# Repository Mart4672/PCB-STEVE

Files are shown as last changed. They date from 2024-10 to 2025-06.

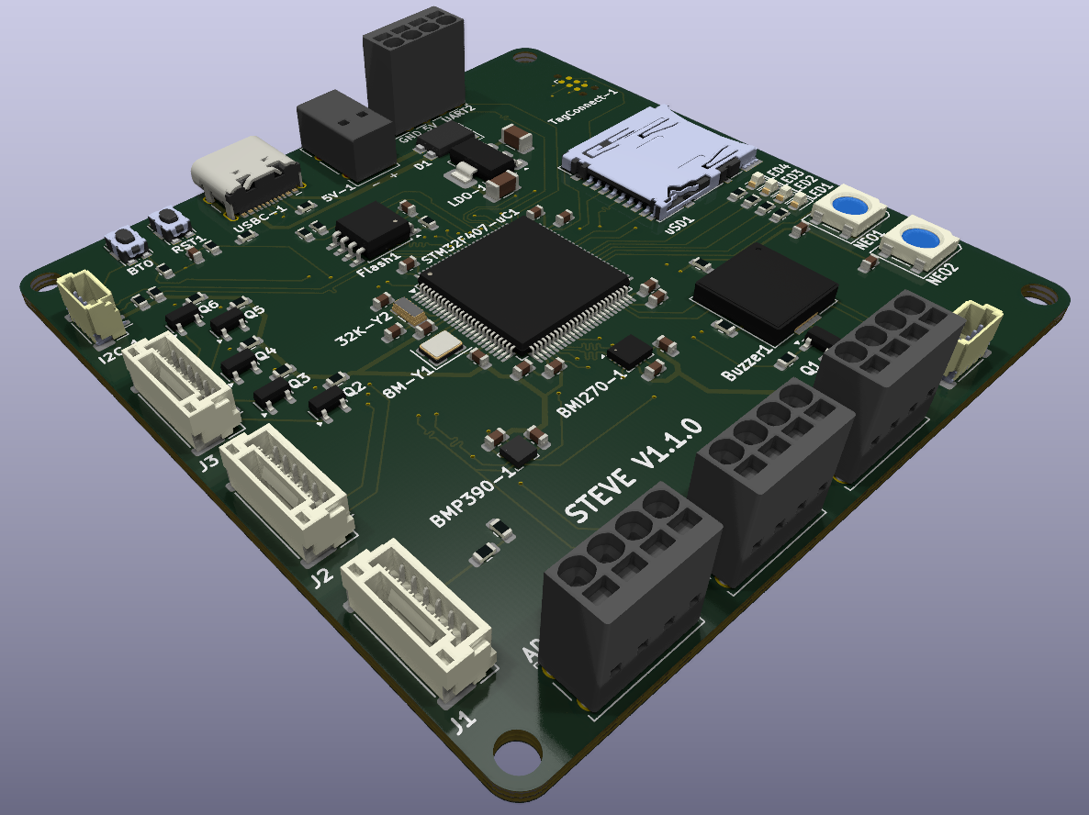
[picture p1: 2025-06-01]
hardware/share/STEVE_V1.1.0/STEVE-1.1.0_3D_Front_45deg.png

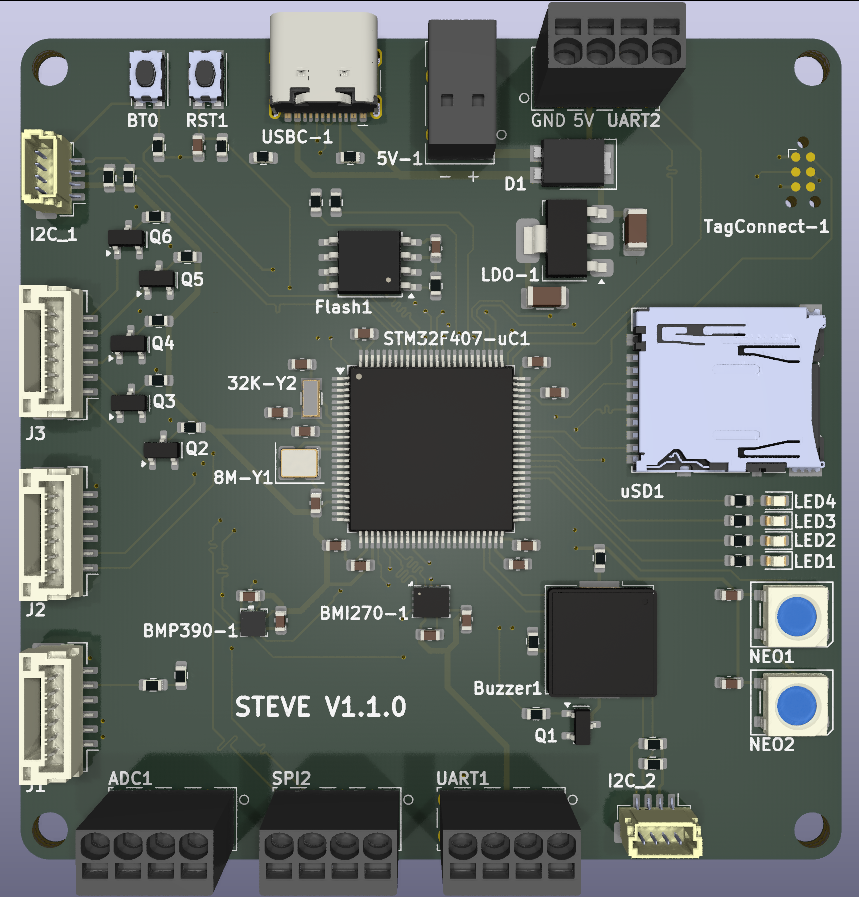
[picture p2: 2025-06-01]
hardware/share/STEVE_V1.1.0/STEVE-1.1.0_3D_Front.png

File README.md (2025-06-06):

# PCB-STEVE
STM32F4 based Flight Computer Development PCB

STEVE, the name of this flight computer, is an acronym:
*Starter Testbed for Evolving the Vehicle Electronics*

As the name implies, the intention of STEVE is to be a testbed circuitboard for proving out avionics functionality.
STEVE is very much a development board as this is the first STM32 PCB that I have designed.

Future versions of STEVE will have a focus on exapnding a flight vehicle's envelope 
(Starter Testbed for Expanding the Vehicle Envelope)

STEVE is intended to be used on a flight vehicle such as a model rocket but can also be used in static environments such as a ground test stand.

## STEVE Version 1.1.0 Hardware Features
- 70 x 70 mm, 6 layer board with all components on one side for ease of manufacturing
- 1 STM32F407 Microcontroller
    - (STM32F407VGT6 is the specific SKU being used)
    - 1024 KB (1MB) of internal flash memory
    - 192 (112+16+64) KB of system RAM
- Reset and Boot buttons
- USB-C input for programming the microcontroller
    - the GCT USB4105-GF-A connector is allegedly rated for 5A
    - also usable for power when not connected to the PSM board
- Terminal block for 5V regulated input
- Micro SD card
- Winbond W25Q 128 Mbit (16 MB) external flash storage
- 1 BMI270 Inertial Measurement Unit (IMU) connected over SPI
- 1 BMP390 Barometric Pressure Sensor connected over SPI
- A 2x5 1.27mm pitch debug header
- A 32.768 kHz Low Speed External Crystal Oscillator
- A 8 MHz High Speed External Crystal Oscillator
- A TI TLV1117 1A 3.3V Output Linear Regulator
- A dedicated telemetry modem connection
    - uses screwless terminal blocks or a JST-GH connector
        - (each JST-GH connection is rated for 1A and the RFD900 has a max draw of ~1A at 5V)
    - GND, 5V, and UART signals (RX and TX) are present
    - placed close to both the USB-C and Regulated 5V power inputs
- 2 JST-SH 4 pin connectors for I2C
    - allows for easy hardware development for I2C devices (load cells, GNSS, etc)
- 1 passive buzzer (passive buzzers allow for different beep noises)
- 4 standard LEDs
- 2 WS2812 (NeoPixel) Addressable LEDs
- Additional GPIO and bus pins broken out
    - SPI2 (also used for BMP390) pins
    - UART1 pins
    - 2 ADC (12-bit) capable pins
    - Uses screwless terminal blocks
- Connectors for PSM board signals (3 x 6 pin connectors)
    - Uses JST-GH connectors
    - Servo PWM signals (4)
    - Mosfet gate signals (5)
    - Mosfet continuity signals (5)
    - Battery #1 Voltage sense line

## Future Updates

### Future STEVE Updates
- use a 3.3V plane on layer 5 (some signals ok) if doing a 6 layer board with components on 1 side
- move the 5V components to the same area
- make the board smaller (60 x 60 mm)
- consider moving the complicated components (BMI, BMP, WS2812) to a separate board
    - probably a bad idea since creating a simple daughter board with Standard PCBA would cost at least (10 PCB + 30 PCBA + 25 shipping) = $65
    - using Economic PCBA only saves ~$25
- give serious consideration to creating a STEVE revision with the PSM circuitry on the same board
    - keep in mind that any board orders also have tarrifs, taxes, and shipping applied, which can easily double the initial PCB/PCBA cost
- use a PMOS mosfet for reverse polarity protection
- add an RJ45 connector to utilize the ethernet capabilities of the STM32F407 (this might be part of a completely different board design)

## Using/opening this project on a different machine

- open the project file in KiCad

On the top bar, the following thing needs to be updated based on the machine you are using:
- Preferences > Configure Paths
Add an enironment variable with a name of:
CURRENT_PROJ_DIR
The value of the enirnment variable should be:
your-repo-dir-path/PCB-STEVE/hardware

On the top bar, the following things should not need to be updated but both use the CURRENT_PROJ_DIR variable 
- Preferences > Manage Symbol Libraries > Project Specific Libraries (tab)
- Preferences > Manage Footprint Libraries > Project Specific Libraries (tab)

## PCB Ordering Notes

#### STEVE V1.1.0 
STEVE V1.1.0 is a 6 layer PCB that uses vias as small as 
0.3mm (hole size) / 0.45mm (overall via diameter)

On JLC's website, 6 layer boards use the "Advanced PCB/PCBA service".
This has different default options from the standard service

Nonstandard options chosen for the advanced PCB service:

- (optional) Specify Stackup > No requirement
- Mark on PCB = 2D barcode (Serial Number)
    - 2D barcode Only | QR Code | STEVE_V1-1-0_SN | Remove Unique Number | 0001 
        - 8*8mm (5x5 also ok) | Specify Position (No Requirement is ok too)

Advanced Options
- $0.71 Blank Box

PCB Assembly Options
A board with 6 or fewer layers and single sided assembly qualifies for 
JLC's Economic PCBA
https://jlcpcb.com/capabilities/pcb-assembly-capabilities
See the above link for Economic PCBA constraints such as
- only supporting green silkscreens
- only supporting the ENIG finish

STEVE 1.1.0 is a 70 x 70mm board; using Standard PCBA auotmatically sets the 
board size to at least 70x70mm for adding edge rails/fiducials.
"The board size would be modified to be 80*70mm for Standard PCBA due to adding two 5mm edge rails on the shorter sides"

Nonstandard PCBA options chosen:
- PCBA Qty = 2 (can choose 2+ based on component availibility)
- Edge Rails/Fiducials = Added by JLCPCB (default)
- Confirm Parts Placement = Yes

Advanced Options
- Photo Confirmation = Yes (Not available for Economic)
- Conformal Coating (+cleaning) = No (can choose yes for future boards)
    - Not available for Economic PCBA
- Packaging = ESD+Cardboard (Cardboard is ok too)
- Solder Paste = Sn96.5/Ag3.0/Cu0.5 (Do NOT use Bismuth/Bi solder)
- The "Bake Components" option is not available for Economic PCBA
    - Will need to use the Standard PCBA service or omit the WS2812 LEDs (C2761795) from being assembled since they are moisture sensitive
- The BMI270 and BMP390 also require Standard PCBA

"Note: The setup fee is $25 per assembly side for Standard PCBA."

Stencil Order Options
- No stencil being ordered
    - If boards with many small pitch components (ex: STM32) are going to be assembled, a reflow oven is strongly recommended
    - if a stencil is ordered, make sure to get it cut to size to save on shipping costs

## Other Notes
- Don't use special characters such as "µ" for part designators, footprints, or values as this can cause issues with processing the bom and positions (CPL) files.

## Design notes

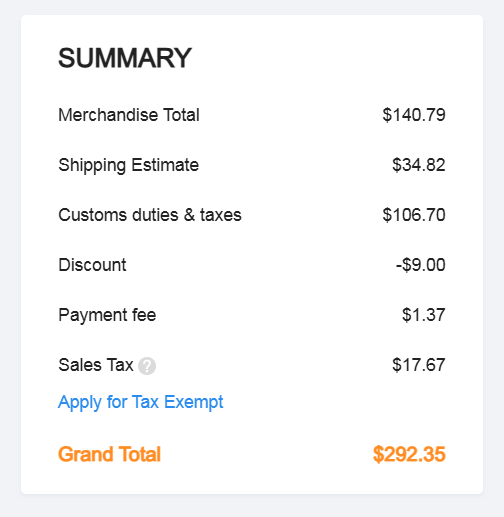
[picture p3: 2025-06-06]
hardware/production/STEVE-1.1.0/STEVE-1.1.0-Quote-JLC/2025-06-01_JLC_PCBA_Quote_Part4_grand_total.png

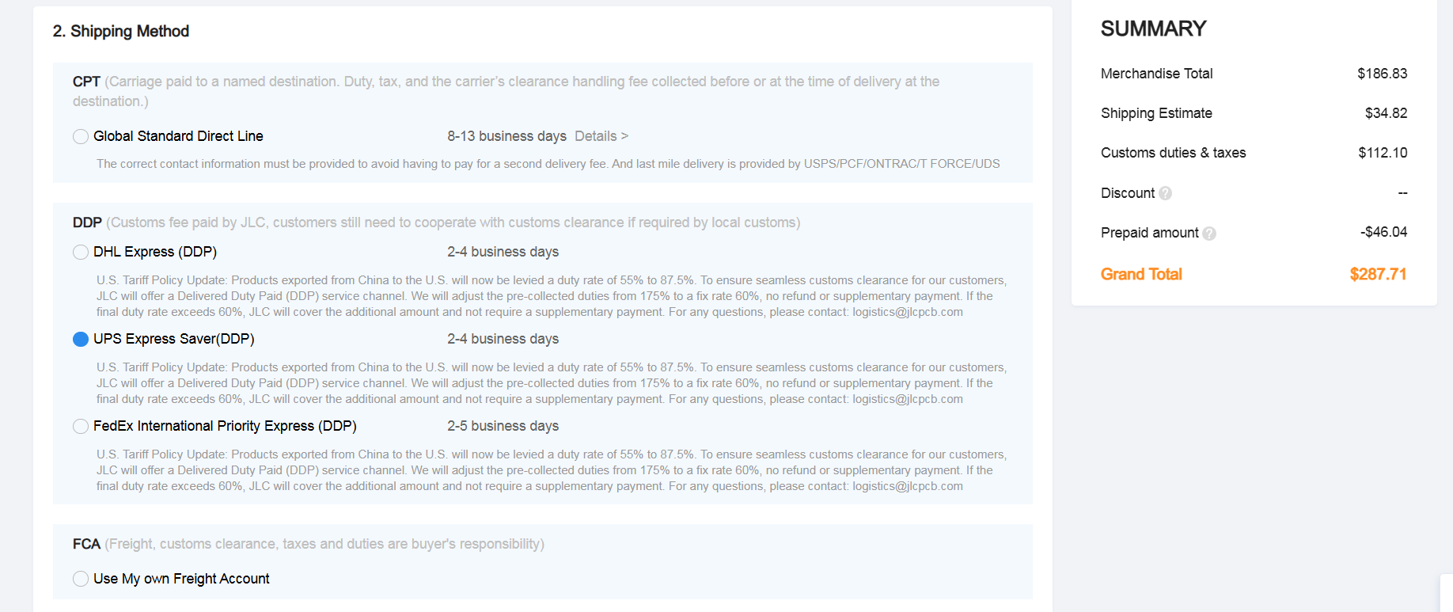
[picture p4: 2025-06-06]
hardware/production/STEVE-1.1.0/STEVE-1.1.0-Quote-JLC/2025-06-01_JLC_PCBA_Quote_Part3_tarrifs.png

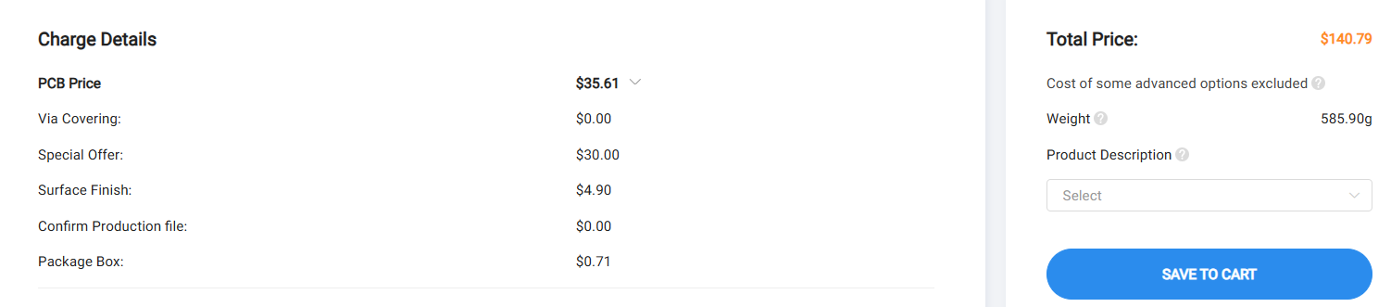
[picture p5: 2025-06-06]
hardware/production/STEVE-1.1.0/STEVE-1.1.0-Quote-JLC/2025-06-01_JLC_PCBA_Quote_Part1.png

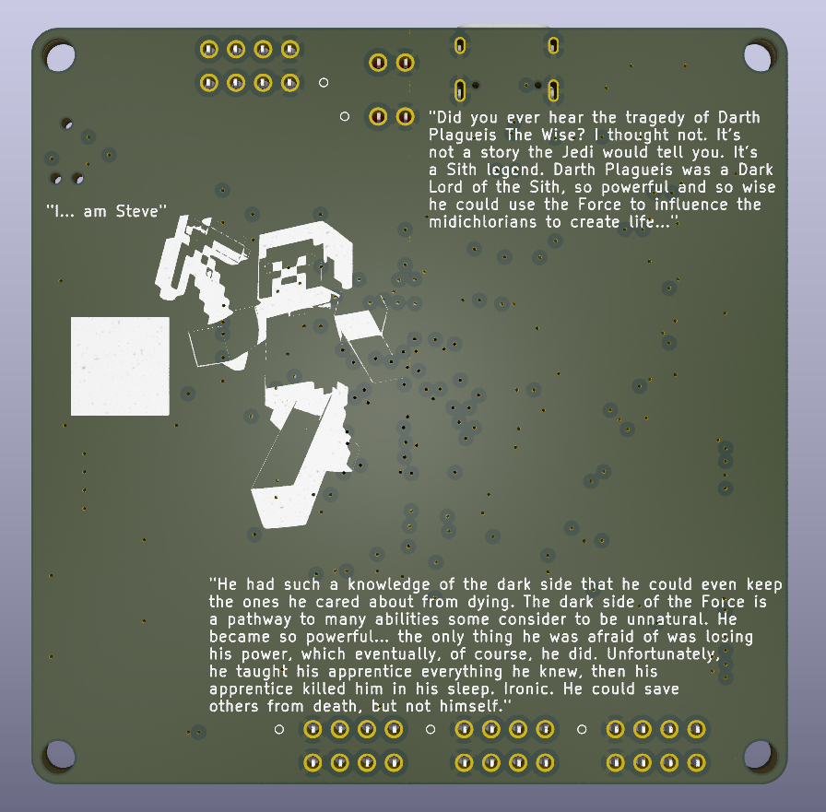
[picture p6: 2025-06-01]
hardware/share/STEVE_V1.1.0/STEVE-1.1.0_3D_Back.png

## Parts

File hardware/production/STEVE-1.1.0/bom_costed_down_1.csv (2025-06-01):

Designator | Footprint | Quantity | Value | LCSC Part #
32K-Y2 | Crystal_SMD_3215-2Pin_3.2x1.5mm_Fixed | 1 | 32.768kHz Crystal 12.5pf C90944
8M-Y1 | Crystal_SMD_3225-4Pin_3.2x2.5mm | 1 | 8MHz Crystal 10pf C400090
BMI270-1 | Bosch_LGA-14_3x2.5mm_P0.5mm | 1 | BMI270 Inertial Measurement Unit C2836813
BMP390-1 | QFN_BMP388_BOS | 1 | BMP390 Barometric Pressure Sensor C2684802
BT0, RST1 | SW_Push_3D_1P1T-SH_NO_CK_KMR2xxG | 2 | Button KMR221G C72443
BUZZER1 | Buzzer_Murata_PKMCS0909E | 1 | Externally Driven Buzzer 1.5-12.5V 4kHz 65dB C910763
C1, C2 | 0603 | 2 | 2.2uF
C10, C11, C27, C28, C29, C30, C31, C32, C33, C7, C8, C9 | 0603 | 12 | 0.1uF
C12 | 0603 | 1 | 4.7uF
C13, C14 | 0603 | 2 | 1.0uF
C25, C26 | 1206 | 2 | 1.0uF
C5, C6 | 0603 | 2 | 5pF
D1 | PDS1040CTL-13_PowerDI-5 | 1 | 10A/5A Schottky Diode Arr C780876
FLASH1 | SOIC-8_5.23x5.23mm_P1.27mm_3D | 1 | W25Q128JVSIQ 128Mb SPI Flash C97521
I2C_1, I2C_2 | JST-SH_BM04B-SRSS-TB_1x04_Vertical_P1.00mm | 2 | JST-SH-4P Vertical C160390
J1, J2, J3 | JST_GH_BM06B-GHS-TBT_1x06-1MP_P1.25mm_Vertical | 3 | JST GH 6P Vertical 1A C189892
LDO-1 | SOT-223-3_TabPin2 | 1 | 3.3V 1A Lin Reg C15578
LED1 | 0603 | 1 | RED
LED2 | 0603 | 1 | YELLOW
LED3 | 0603 | 1 | GREEN
LED4 | 0603 | 1 | BLUE
NEO1, NEO2 | LED_WS2812B_PLCC4_5.0x5.0mm_P3.2mm | 2 | WS2812B RGB LED C2761795
Q1, Q2, Q3, Q4, Q5, Q6 | SOT-23 | 6 | NMOS GSD 350mA 60V C282405
R1, R15 | 0603 | 2 | 100k
R11, R12 | 0603 | 2 | 22
R13, R14 | 0603 | 2 | 5.1k
R16, R17, R18, R19 | 0603 | 4 | 2k
R2 | 0603 | 1 | 4.7k
R20, R21, R22, R26 | 0603 | 4 | 1k
R23, R24, R25 | 0603 | 3 | 220
R3, R4, R5, R6, R7 | 0603 | 5 | 10k
R8 | 0603 | 1 | 422k 1%
R9 | 0603 | 1 | 100k 0.5%
STM32F407-UC1 | LQFP-100_14x14mm_P0.5mm | 1 | STM32F407VGTx Microcontroller C12345
USBC-1 | USB_C_Receptacle_3D_HCTL_HC-TYPE-C-16P-01A | 1 | USB-C Receptacle 16P C3025063
USD1 | microSD_3D_HC_Hirose_DM3AT-SF-PEJM5 | 1 | MicroSD Hirose DM3AT C114218

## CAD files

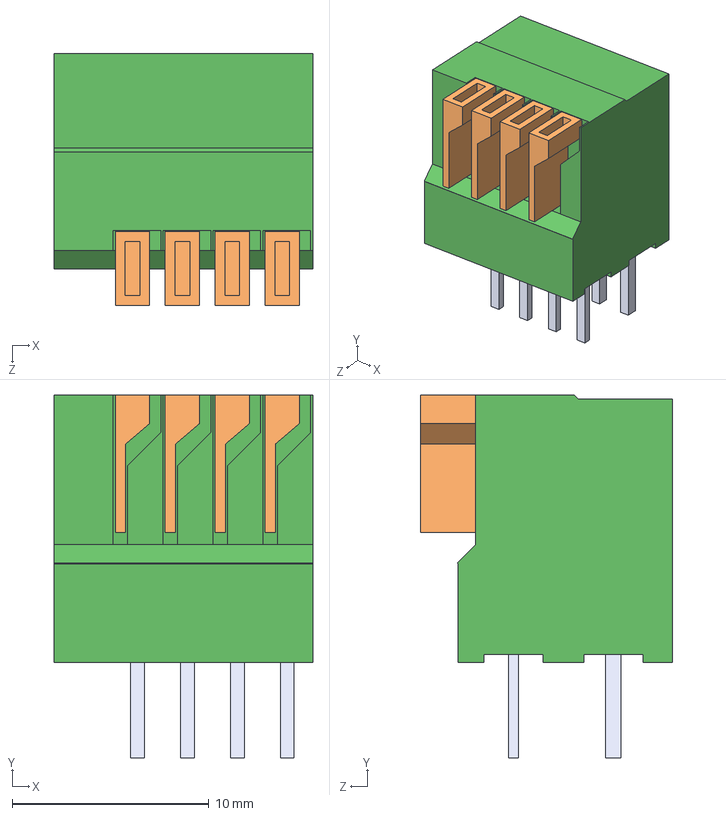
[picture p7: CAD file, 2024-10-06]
hardware/imports/1_2834015_4/1-2834015-4.step
13.2 x 18.5 x 12.8 mm

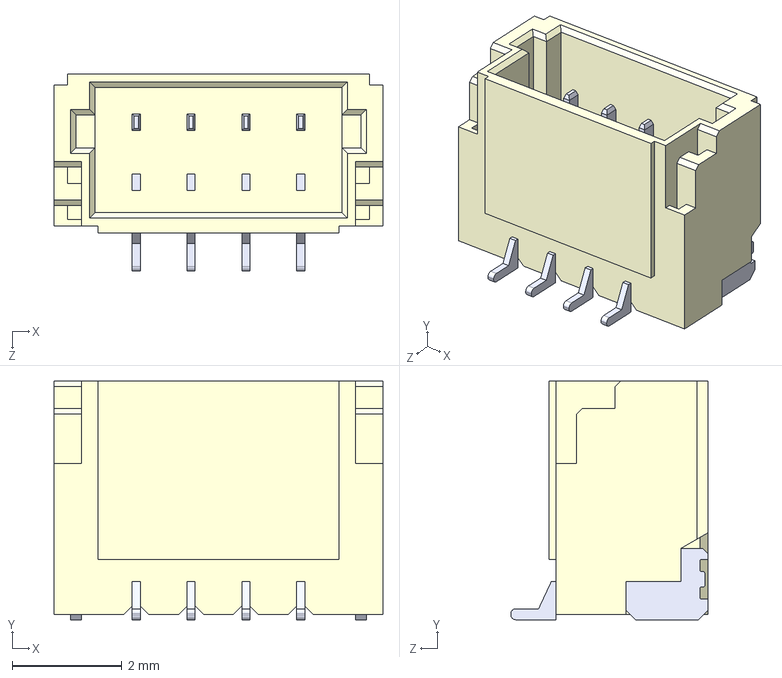
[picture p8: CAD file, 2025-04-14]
hardware/imports/BM04B-SRSS-TB/BM04B-SRSS-TB.STEP
6.00 x 4.35 x 3.60 mm

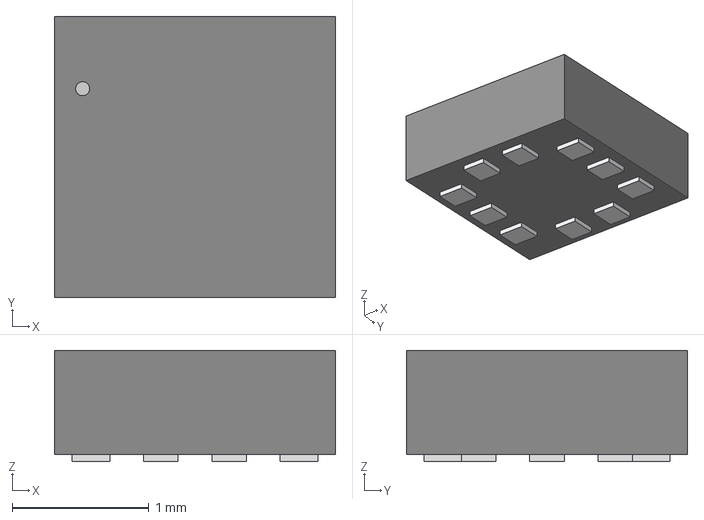
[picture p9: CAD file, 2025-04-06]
hardware/imports/BMP388/QFN_BMP388_BOS.step
2.06 x 2.06 x 0.815 mm

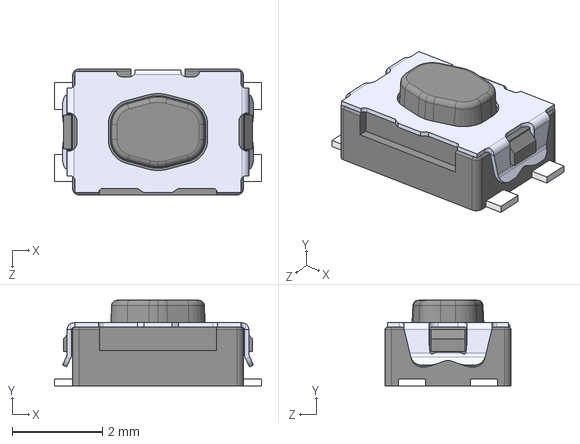
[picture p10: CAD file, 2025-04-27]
hardware/imports/Button_KMR221G_LFS/KMR221G LFS.STEP
4.60 x 1.90 x 2.80 mm

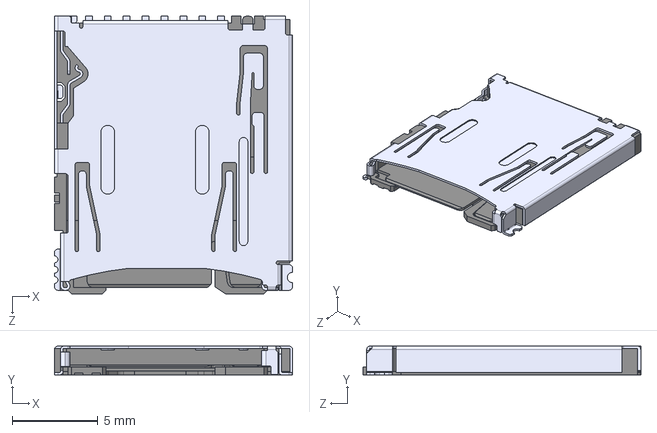
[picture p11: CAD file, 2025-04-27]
hardware/imports/DM3AT_SF_PEJM5/DM3AT-SF-PEJM5.STEP
13.8 x 1.68 x 16.2 mm

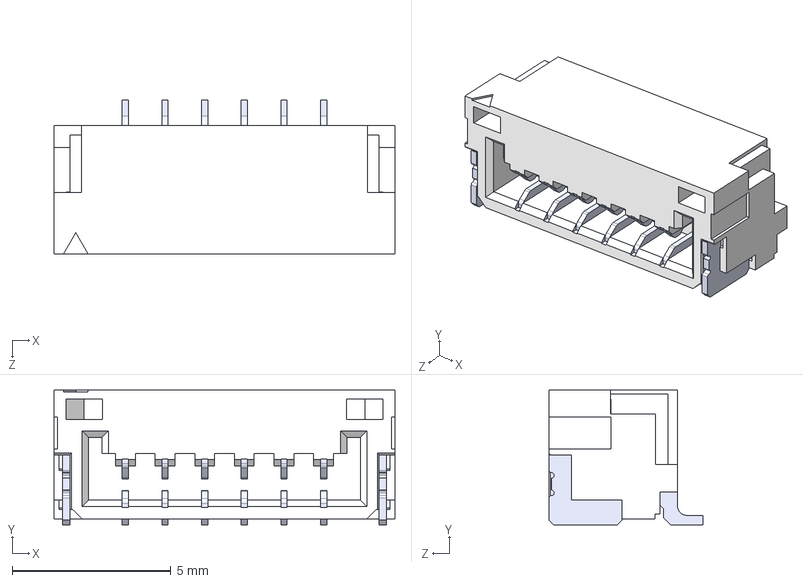
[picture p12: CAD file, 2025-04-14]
hardware/imports/JST-GH-6P-Side_SM06B-GHS-TB/JST-GH-6P-Side_SM06B-GHS-TB.STEP
10.8 x 4.25 x 4.85 mm
SMxB-GHS-TB_06
pin x 6

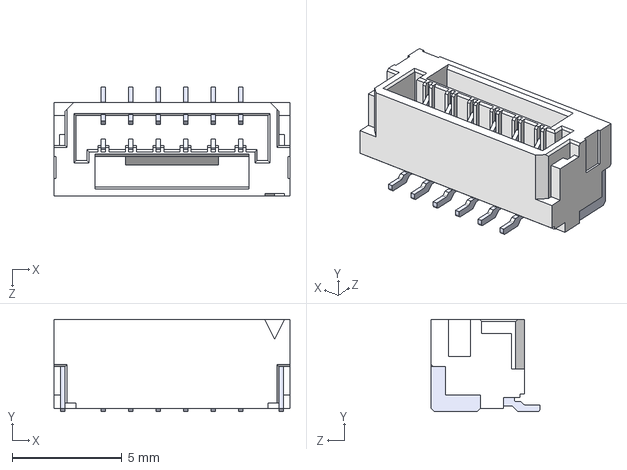
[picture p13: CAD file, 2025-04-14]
hardware/imports/JST-GH-6P-Vertical_BM06B-GHS-TBT/JST-GH-6P-Vertical_BM06B-GHS-TBT.STEP
10.8 x 4.20 x 4.95 mm

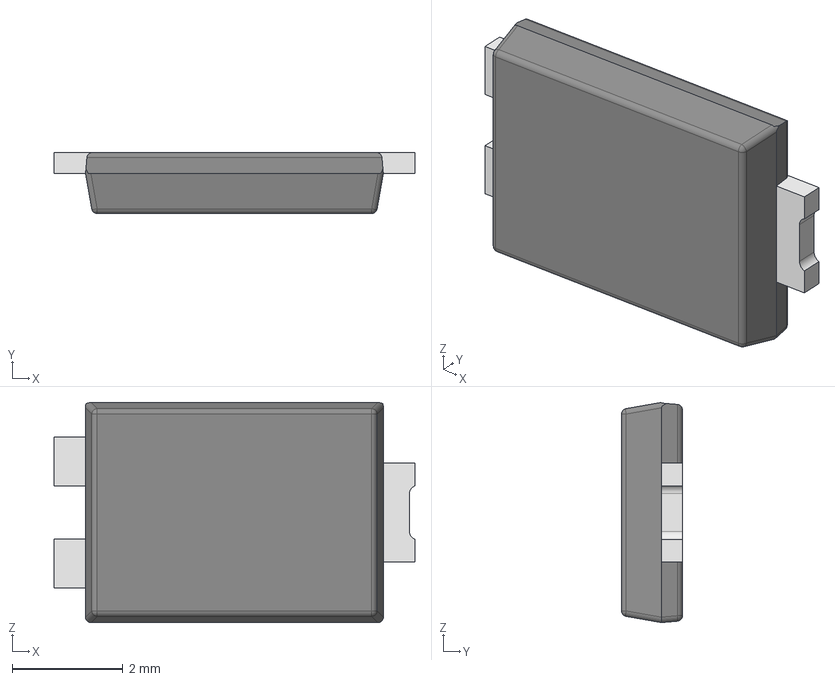
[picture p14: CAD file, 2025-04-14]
hardware/imports/PowerDI-5/PowerDI5.stp
6.51 x 1.10 x 3.97 mm
PD-5 compound
PD-5 LF_0
PD-5 LF

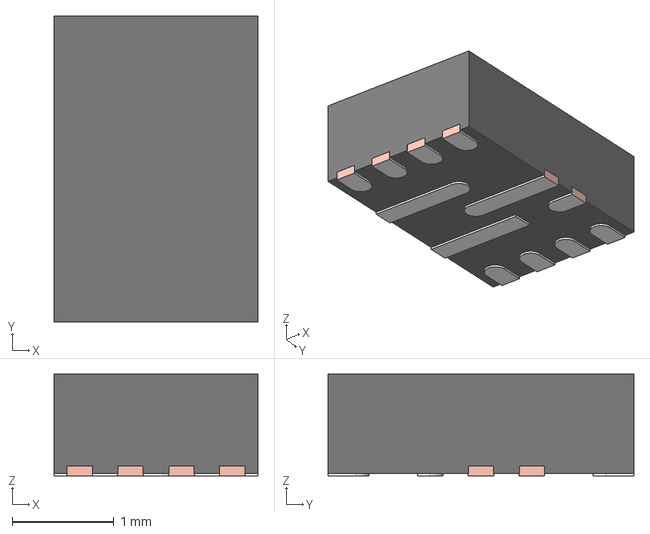
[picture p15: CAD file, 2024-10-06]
hardware/imports/TPS51386RJNR/RJN0012A.stp
2.00 x 3.00 x 1.00 mm
FRAME
MOLD

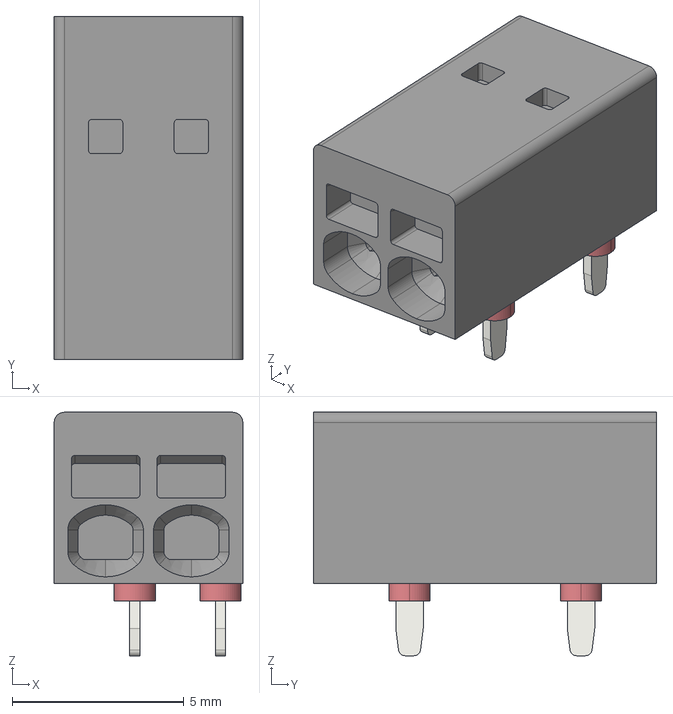
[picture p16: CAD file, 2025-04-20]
hardware/imports/1770885/1770885.stp
5.50 x 10.0 x 7.10 mm

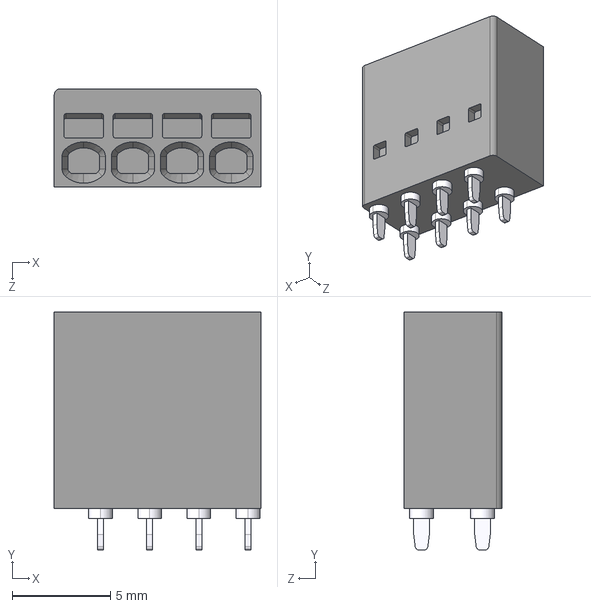
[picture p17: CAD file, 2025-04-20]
hardware/imports/TerminalBlock_1770979_4pos_Vertical/1770979.STEP
10.5 x 12.1 x 5.00 mm

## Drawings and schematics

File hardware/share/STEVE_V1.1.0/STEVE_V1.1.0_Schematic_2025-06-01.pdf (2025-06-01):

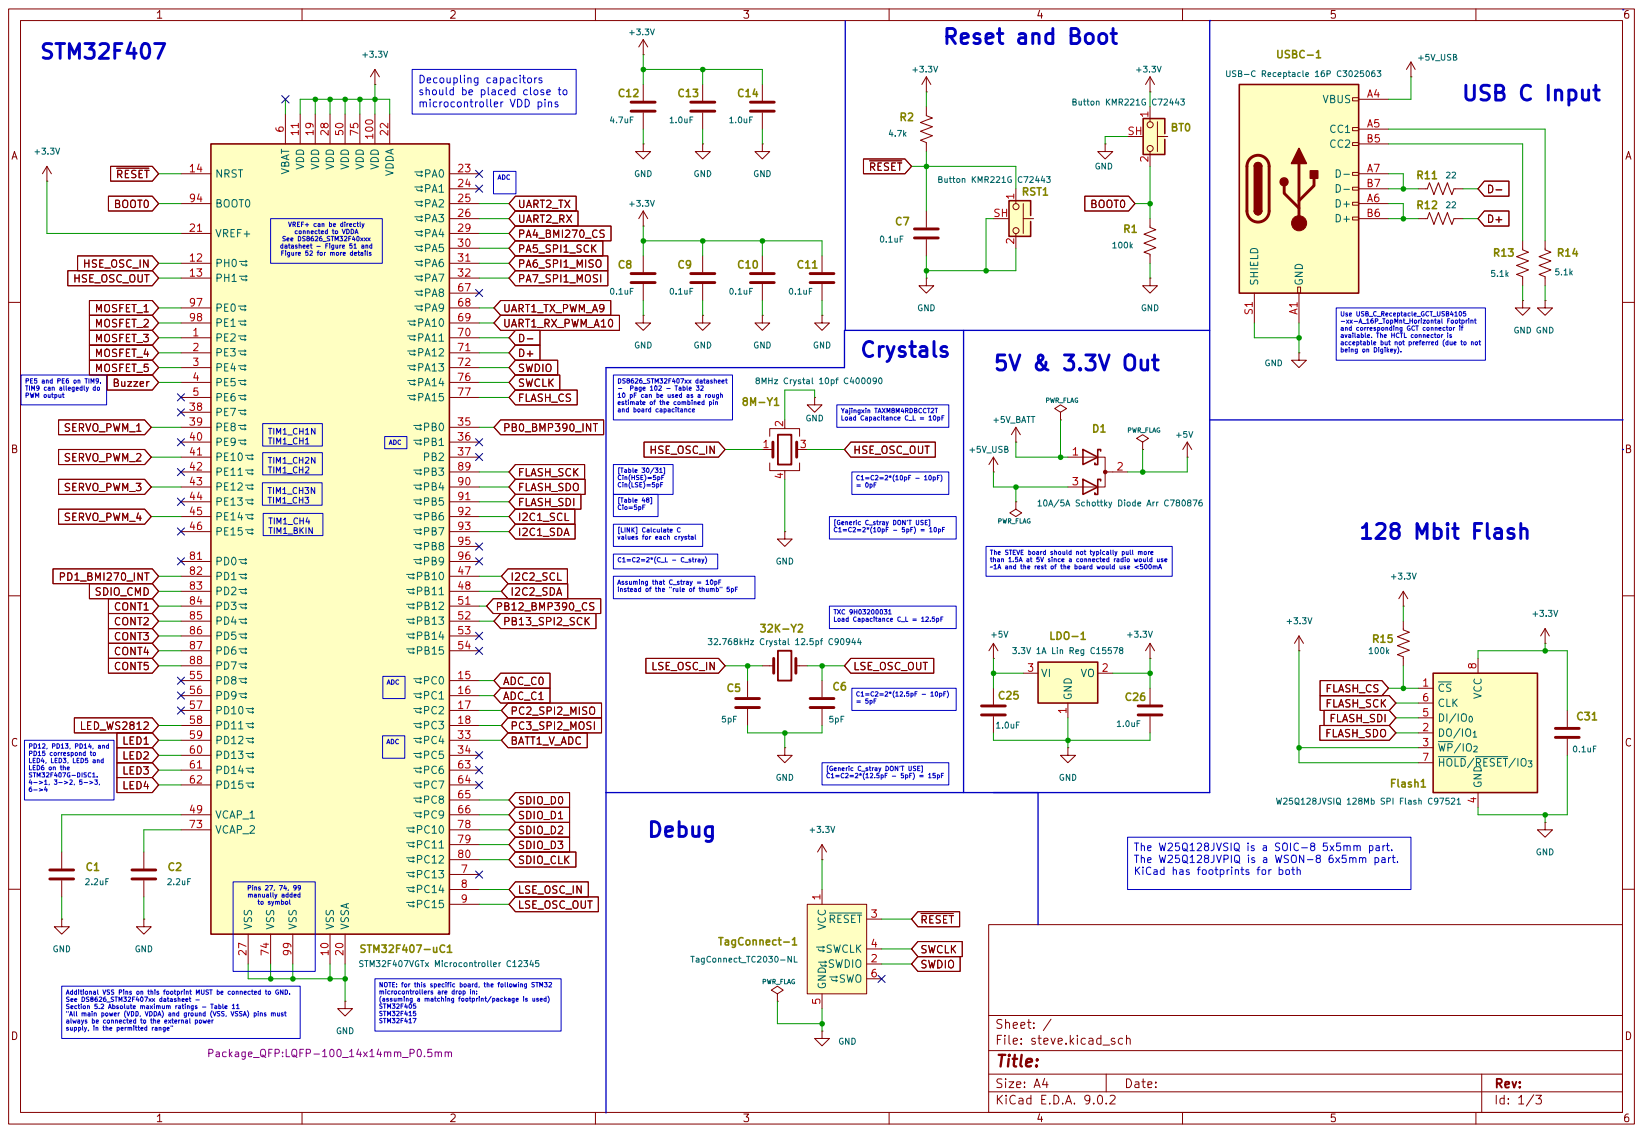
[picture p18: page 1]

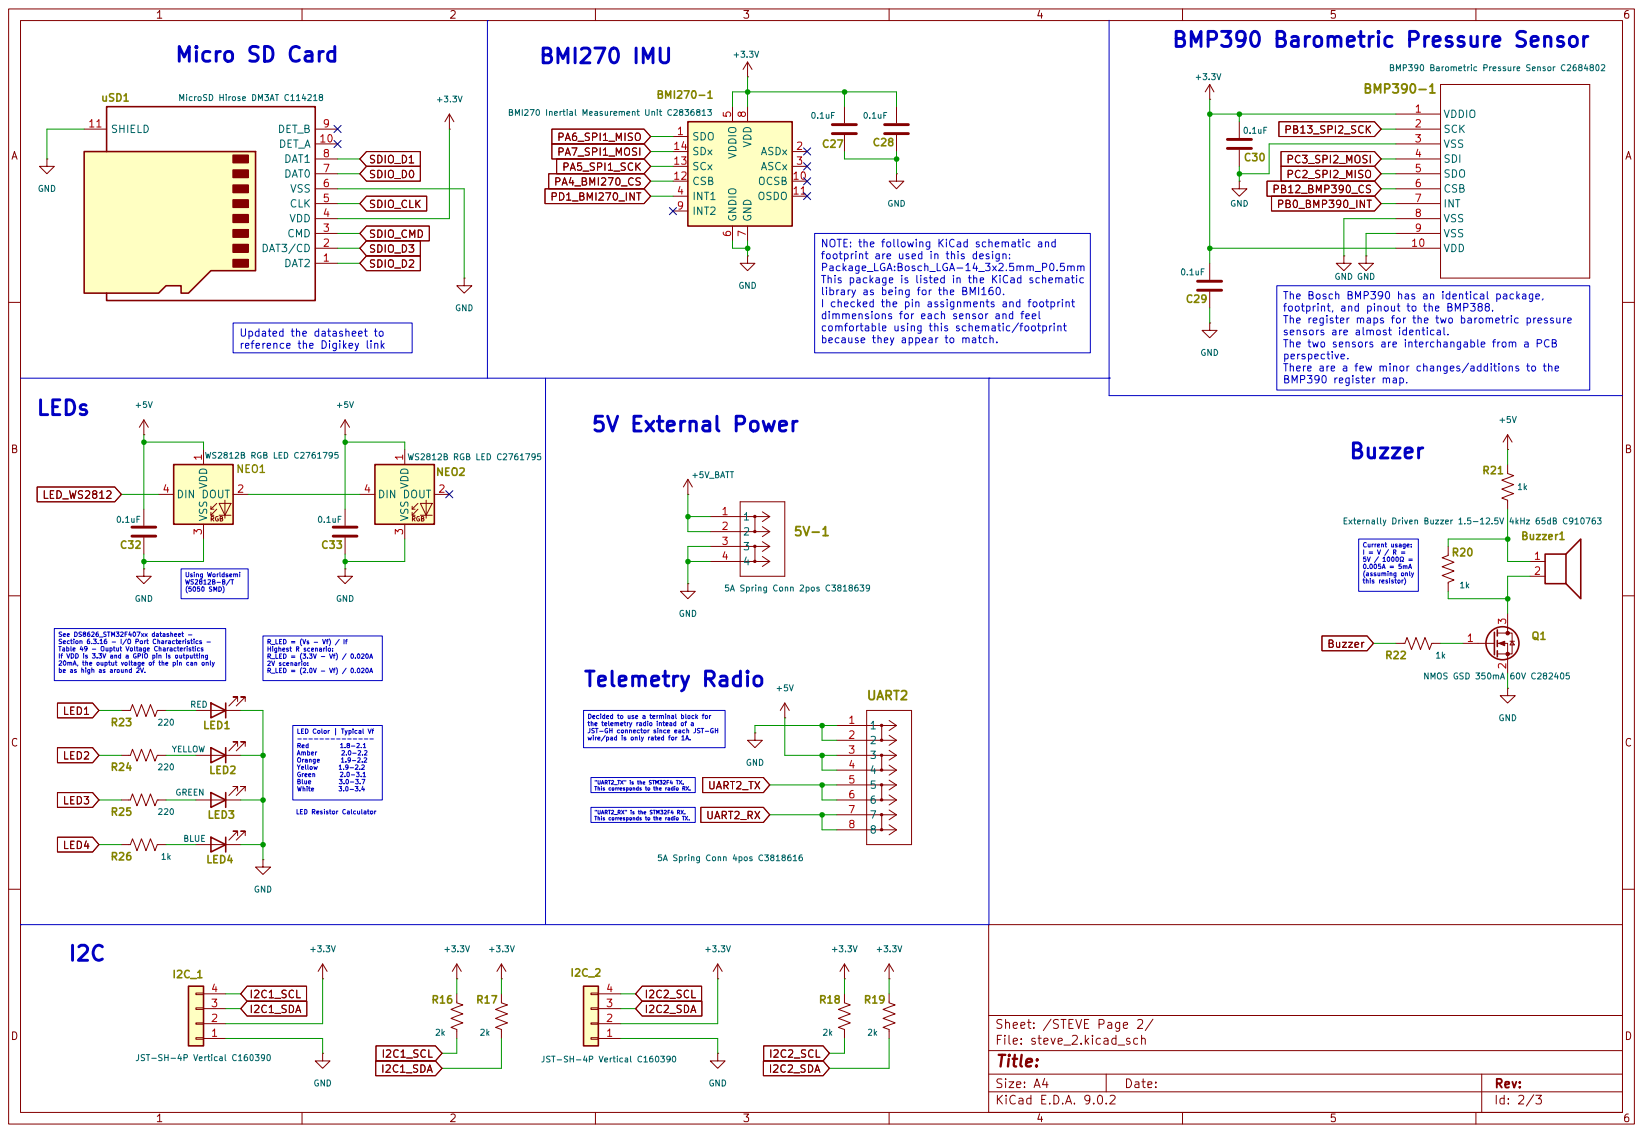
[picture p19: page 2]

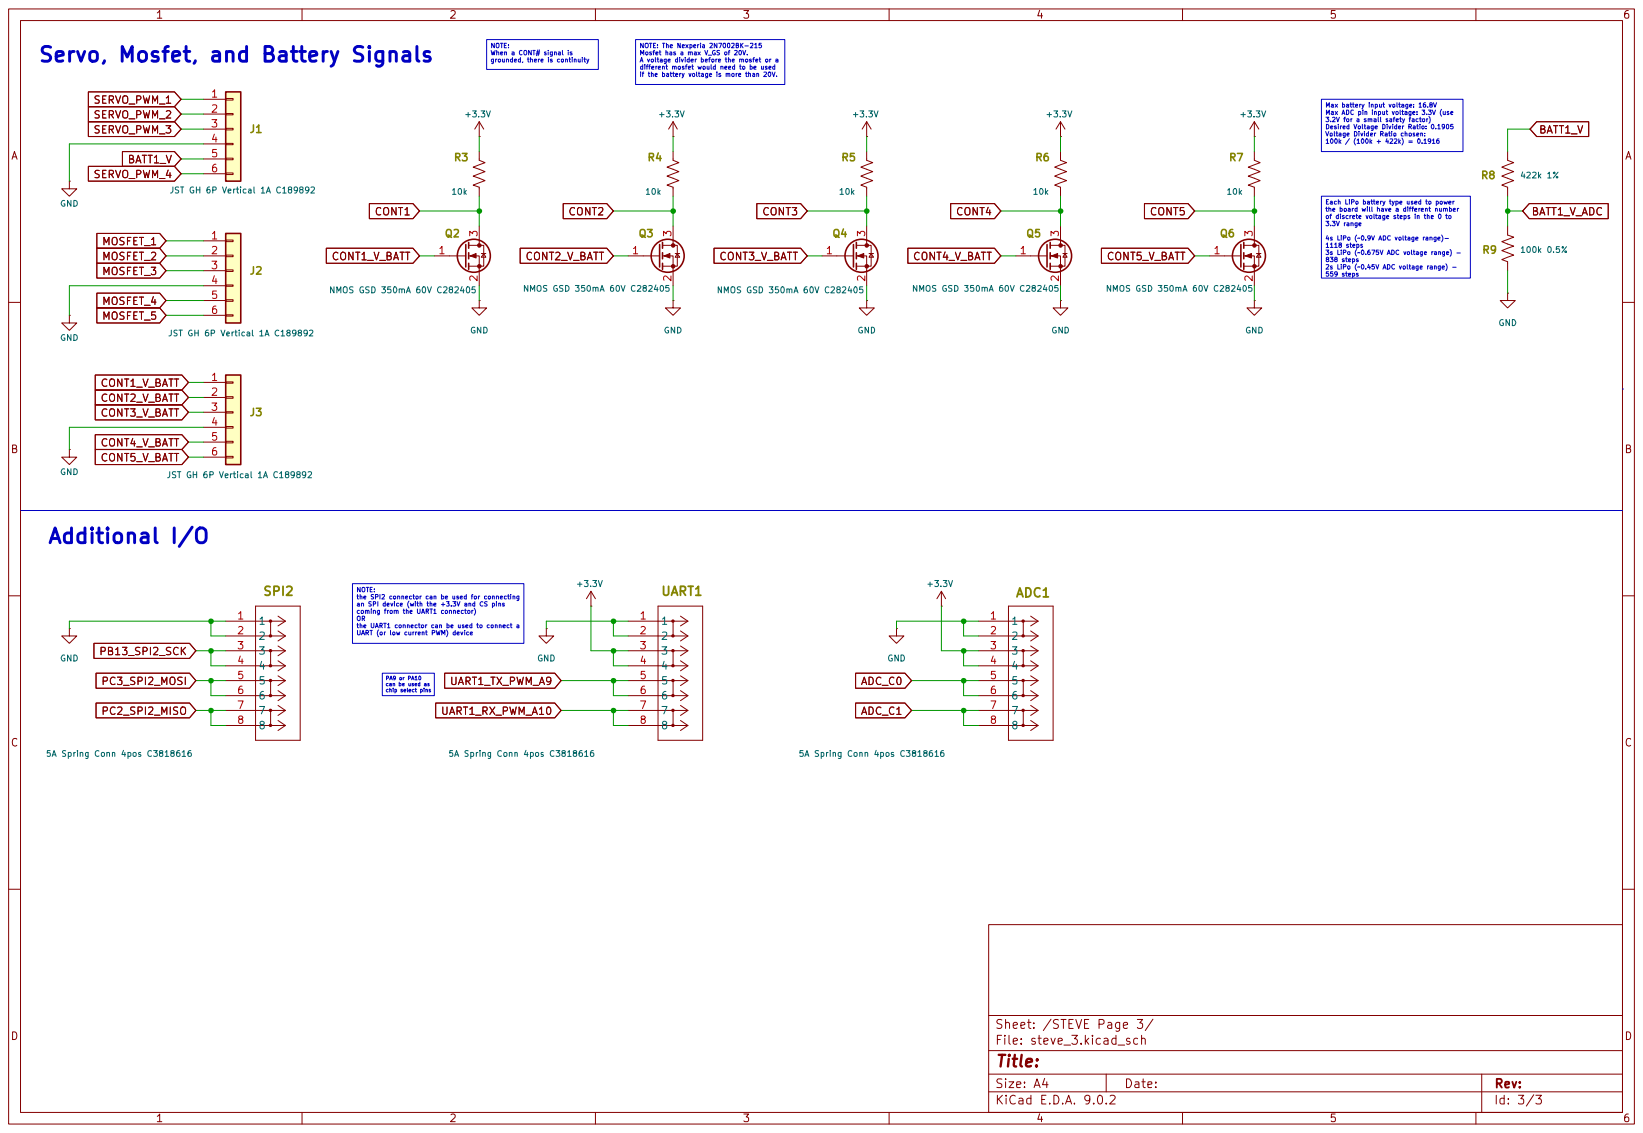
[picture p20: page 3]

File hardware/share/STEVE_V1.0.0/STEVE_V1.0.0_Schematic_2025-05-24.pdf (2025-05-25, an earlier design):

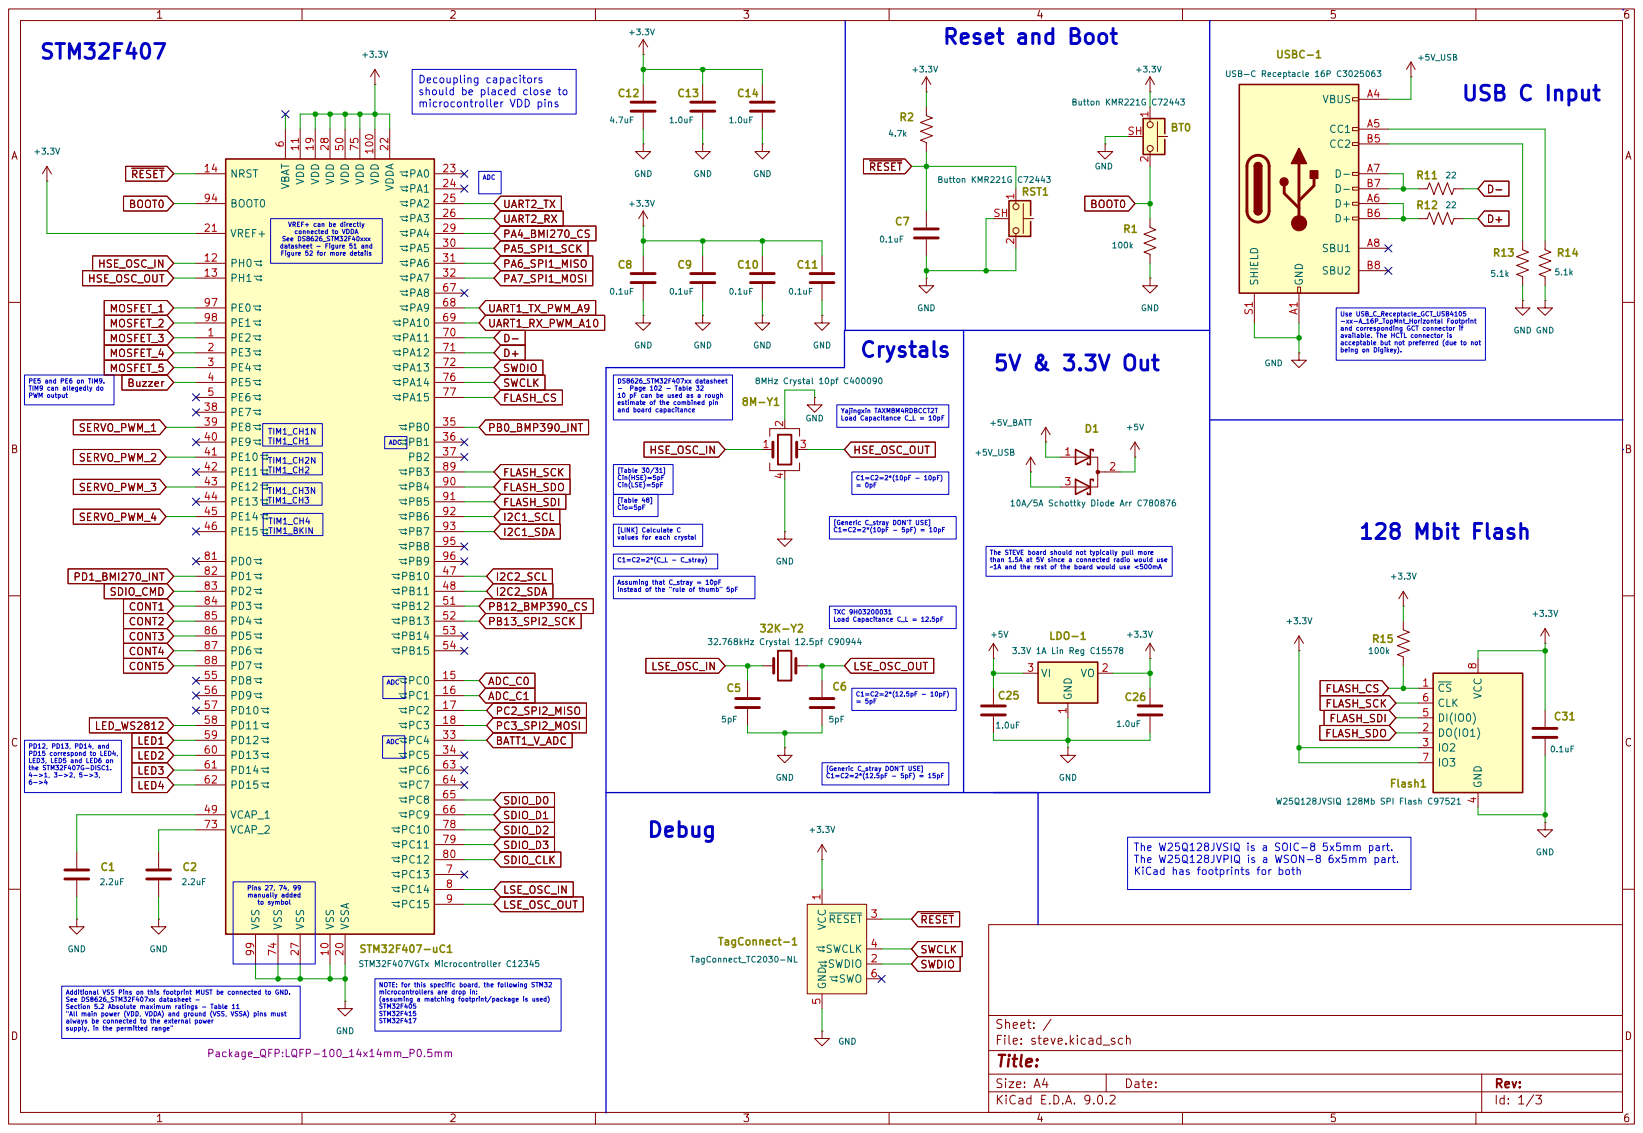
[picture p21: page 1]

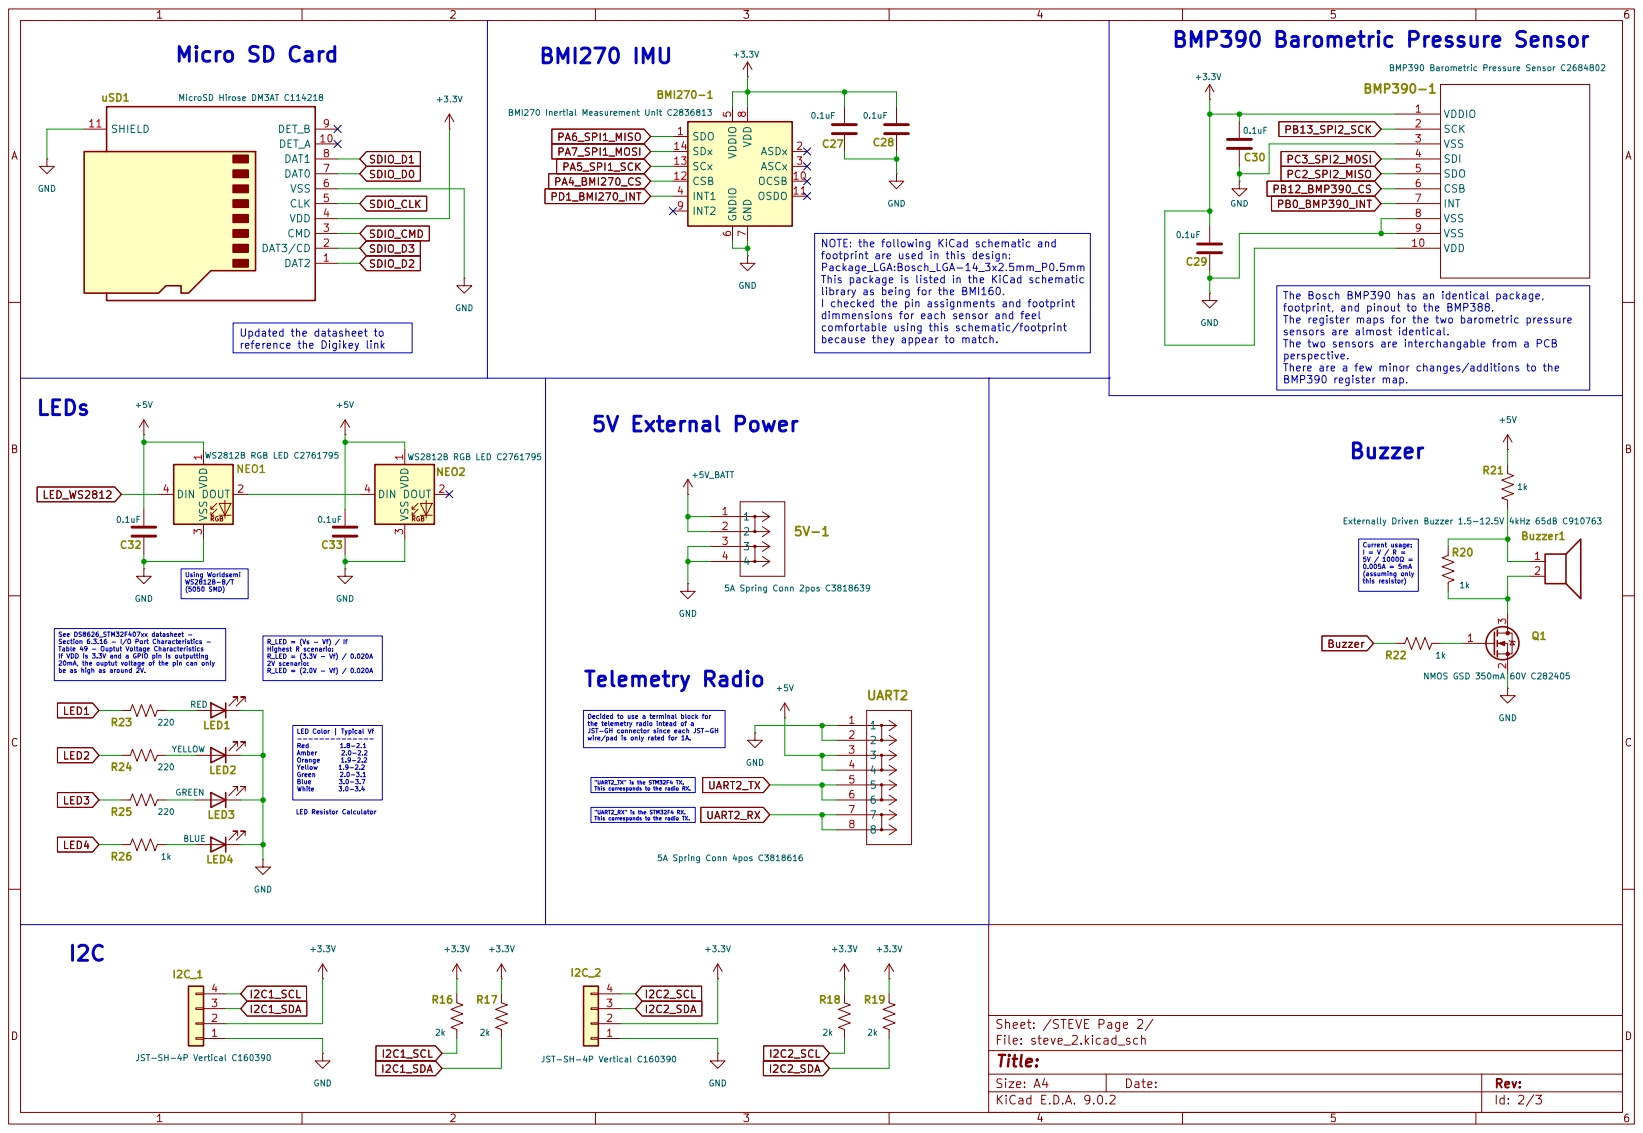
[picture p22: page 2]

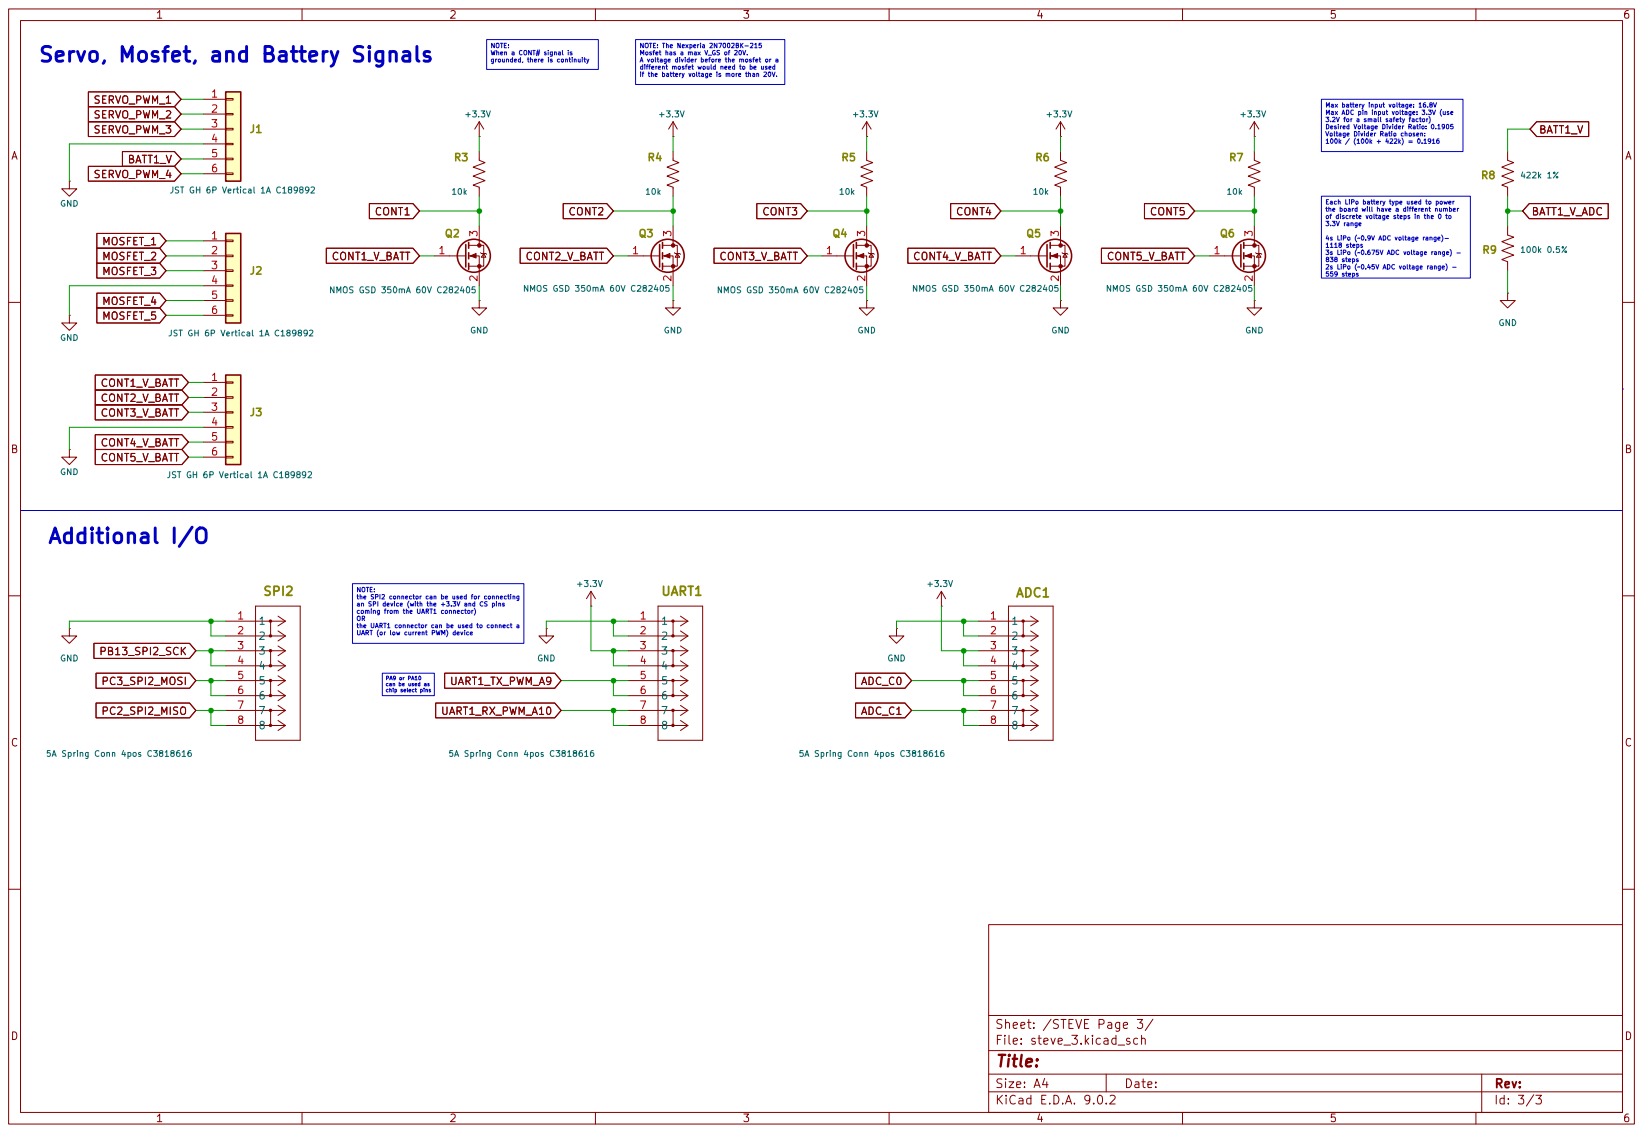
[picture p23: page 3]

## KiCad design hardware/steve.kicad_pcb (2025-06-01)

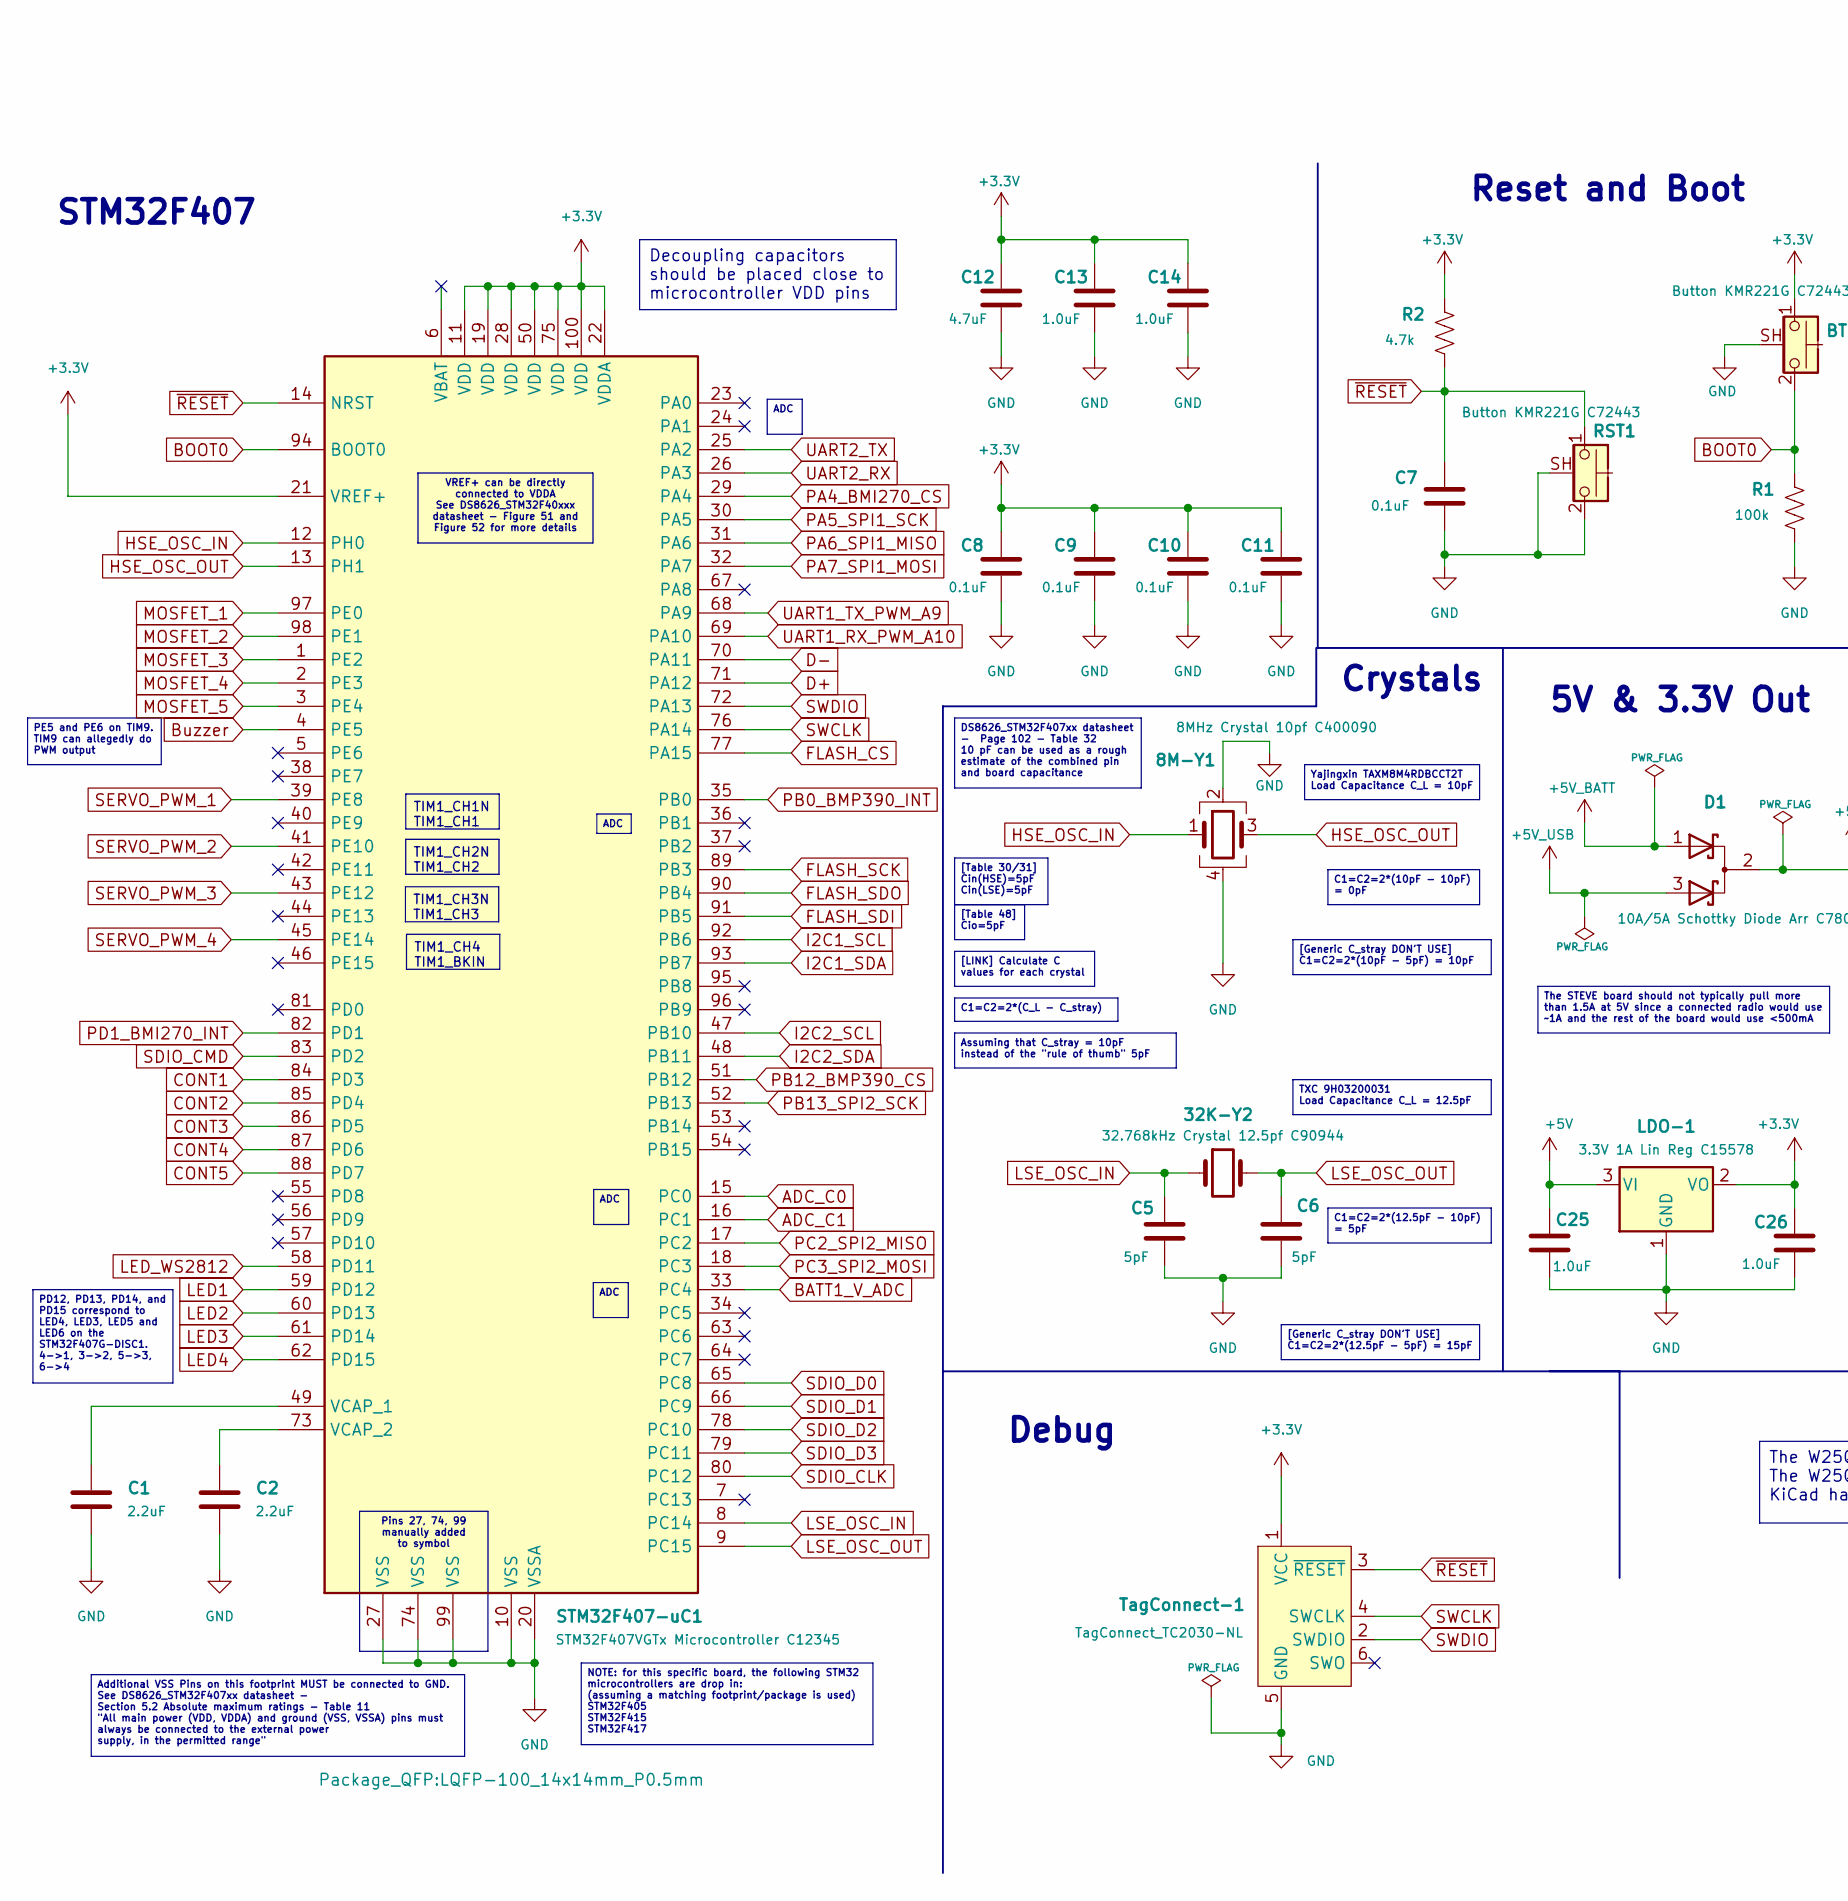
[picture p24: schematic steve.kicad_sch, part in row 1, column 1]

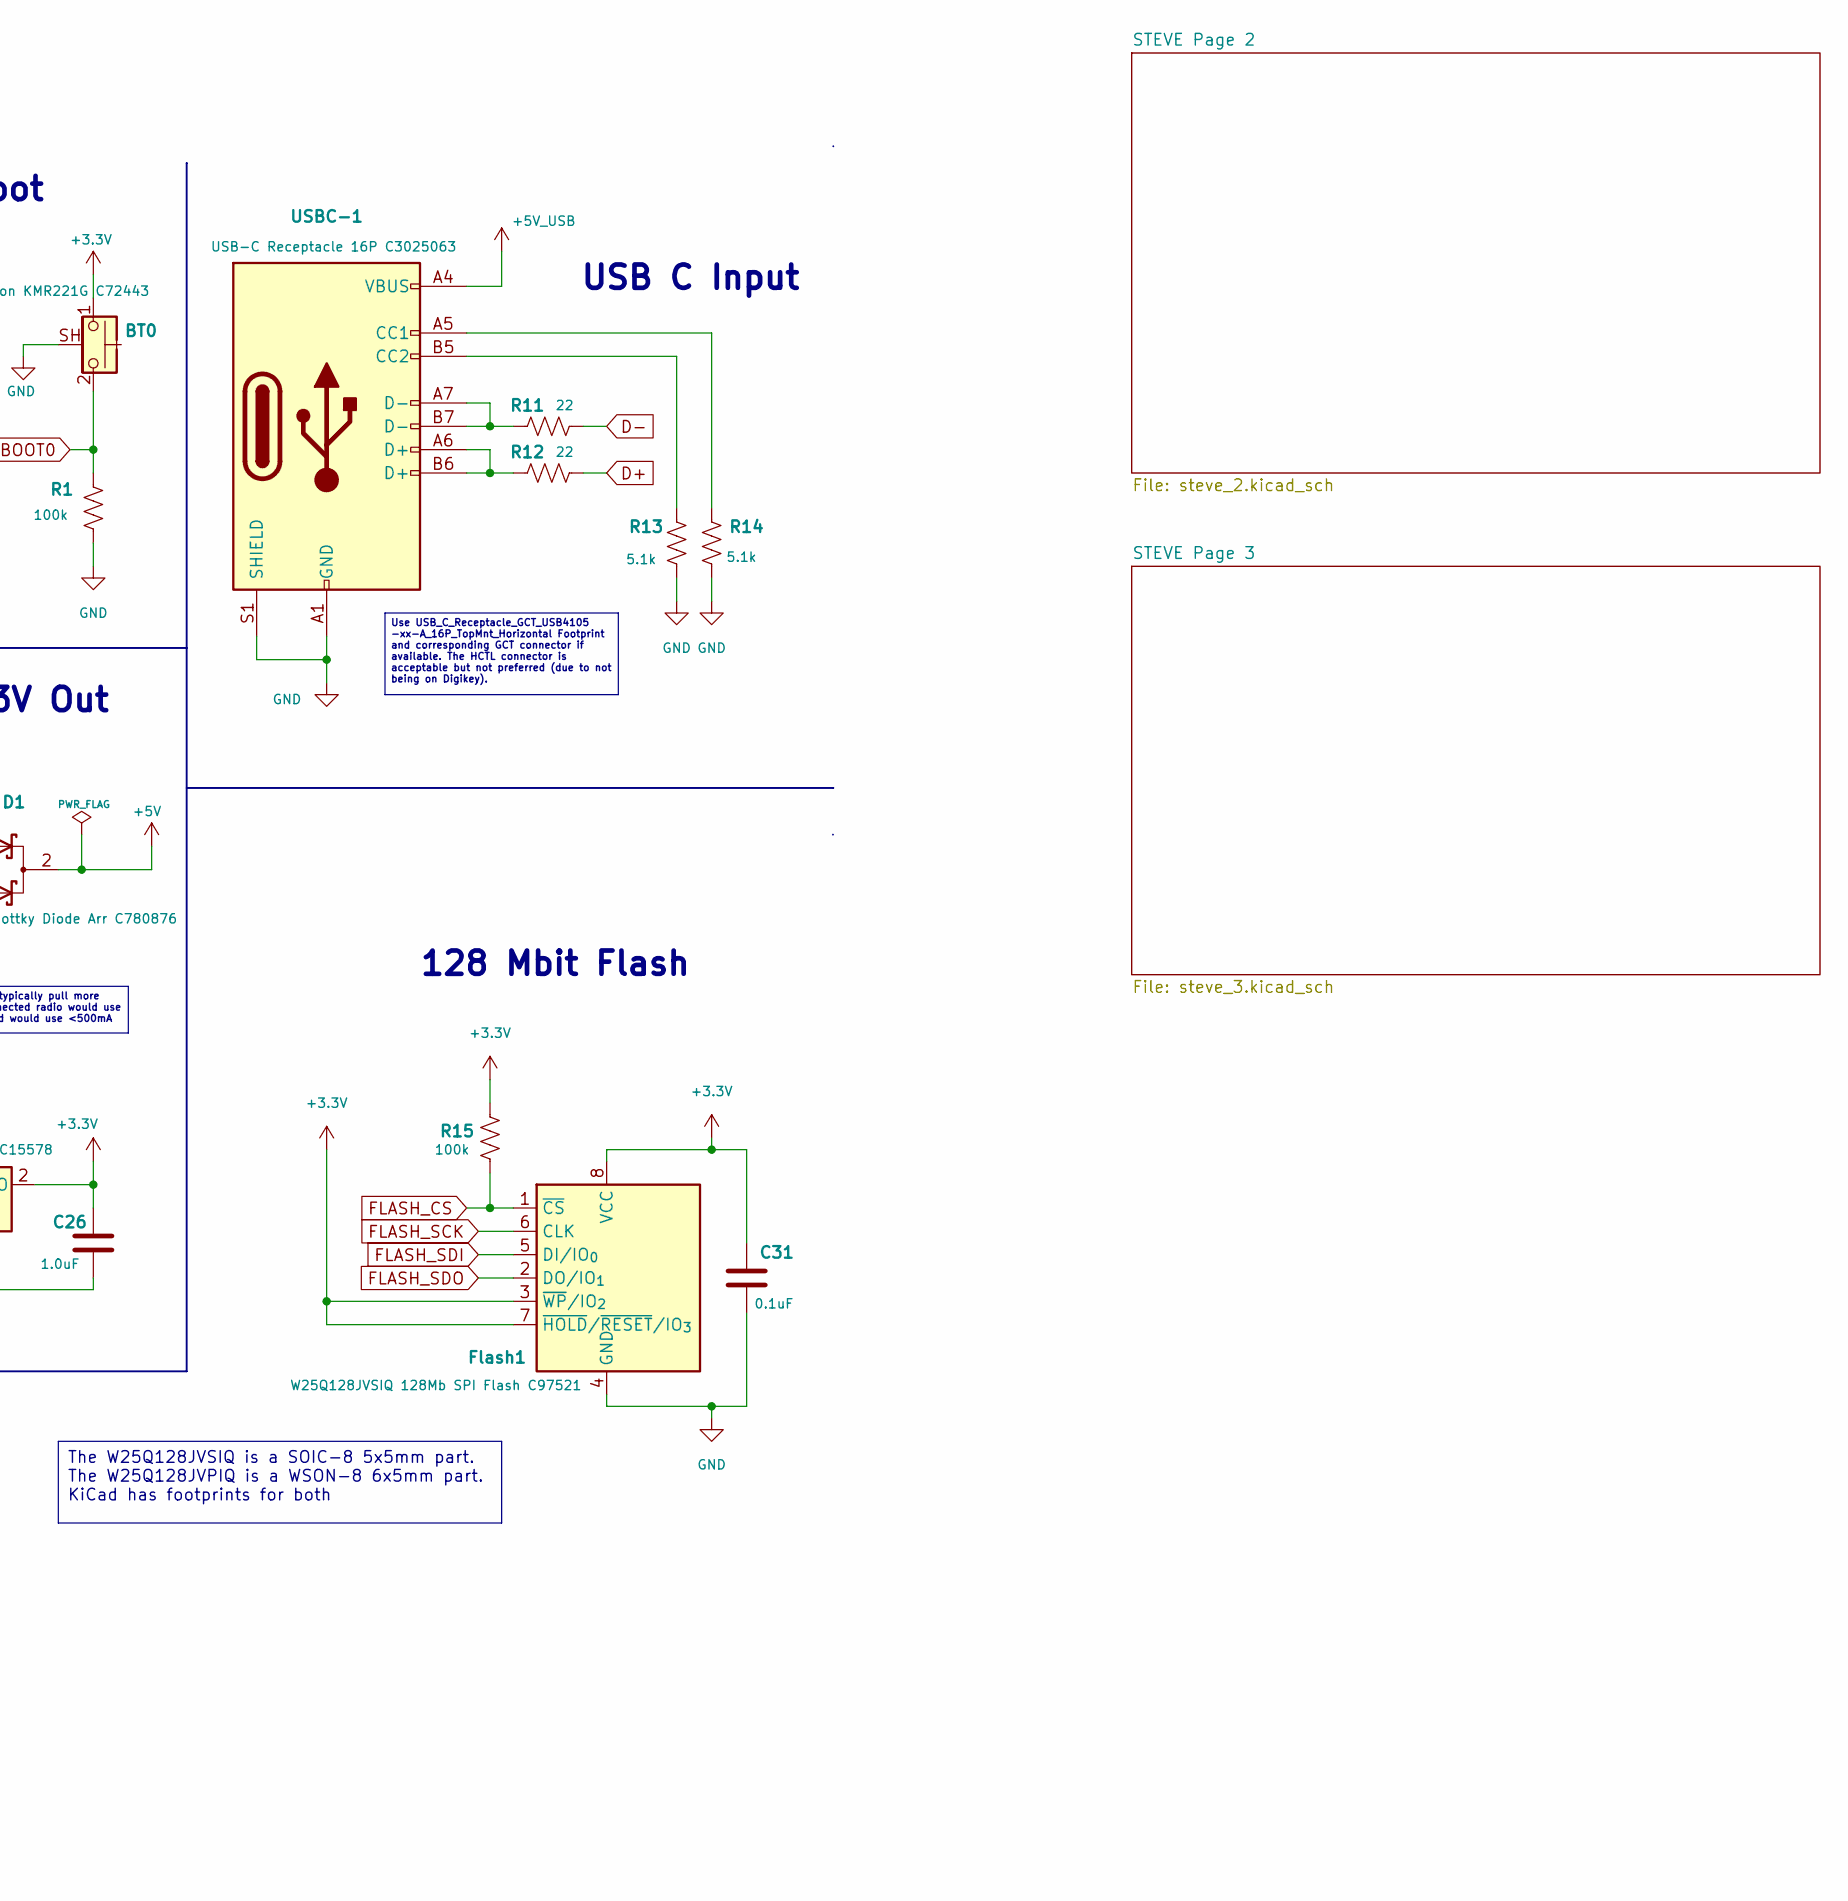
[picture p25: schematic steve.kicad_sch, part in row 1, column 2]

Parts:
8M-Y1: 8MHz Crystal 10pf C400090; Crystal_SMD_3225-4Pin_3.2x2.5mm
32K-Y2: 32.768kHz Crystal 12.5pf C90944; Crystal_SMD_3215-2Pin_3.2x1.5mm
BT0: Button KMR221G C72443; SW_Push_3D_1P1T-SH_NO_CK_KMR2xxG
C1, C2: 2.2uF; C_0603_1608Metric
C5, C6: 5pF; C_0603_1608Metric
C7, C8, C9, C10, C11, C31: 0.1uF; C_0603_1608Metric
C12: 4.7uF; C_0603_1608Metric
C13, C14: 1.0uF; C_0603_1608Metric
C25, C26: 1.0uF; C_1206_3216Metric
D1: 10A/5A Schottky Diode Arr C780876; PDS1040CTL-13_PowerDI-5
Flash1: W25Q128JVSIQ 128Mb SPI Flash C97521; SOIC-8_5.23x5.23mm_P1.27mm_3D
LDO-1: 3.3V 1A Lin Reg C15578; SOT-223-3_TabPin2
R1, R15: 100k; R_0603_1608Metric
R2: 4.7k; R_0603_1608Metric
R11, R12: 22; R_0603_1608Metric
R13, R14: 5.1k; R_0603_1608Metric
RST1: Button KMR221G C72443; SW_Push_3D_1P1T-SH_NO_CK_KMR2xxG
STM32F407-uC1: STM32F407VGTx Microcontroller C12345; LQFP-100_14x14mm_P0.5mm
TagConnect-1: TagConnect_TC2030-NL; Tag-Connect_TC2030-IDC-NL_2x03_P1.27mm_Vertical
USBC-1: USB-C Receptacle 16P C3025063; USB_C_Receptacle_3D_HCTL_HC-TYPE-C-16P-01A

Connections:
+3.3V: BT0.1, C8.1, C9.1, C10.1, C11.1, C12.1, C13.1, C14.1, C26.1, C31.1, Flash1.3 (~WP/IO_{2}), Flash1.7 (~HOLD/~RESET/IO_{3}), Flash1.8 (VCC), LDO-1.2 (VO), R2.1, R15.1, STM32F407-uC1.11 (VDD), STM32F407-uC1.19 (VDD), STM32F407-uC1.21 (VREF+), STM32F407-uC1.22 (VDDA), STM32F407-uC1.28 (VDD), STM32F407-uC1.50 (VDD), STM32F407-uC1.75 (VDD), STM32F407-uC1.100 (VDD), TagConnect-1.1 (VCC); also elsewhere on the board
+5V: C25.1, D1.2 (K), LDO-1.3 (VI); also elsewhere on the board
+5V_BATT: D1.1 (A); also elsewhere on the board
+5V_USB: D1.3 (A), USBC-1.A4 (VBUS), USBC-1.A9 (VBUS), USBC-1.B4 (VBUS), USBC-1.B9 (VBUS)
ADC_C0: STM32F407-uC1.15 (PC0); also elsewhere on the board
ADC_C1: STM32F407-uC1.16 (PC1); also elsewhere on the board
BATT1_V_ADC: STM32F407-uC1.33 (PC4); also elsewhere on the board
BOOT0: BT0.2, R1.1, STM32F407-uC1.94 (BOOT0)
Buzzer: STM32F407-uC1.4 (PE5); also elsewhere on the board
CONT1: STM32F407-uC1.84 (PD3); also elsewhere on the board
CONT2: STM32F407-uC1.85 (PD4); also elsewhere on the board
CONT3: STM32F407-uC1.86 (PD5); also elsewhere on the board
CONT4: STM32F407-uC1.87 (PD6); also elsewhere on the board
CONT5: STM32F407-uC1.88 (PD7); also elsewhere on the board
D+: R12.2, STM32F407-uC1.71 (PA12)
D-: R11.2, STM32F407-uC1.70 (PA11)
FLASH_CS: Flash1.1 (~CS), R15.2, STM32F407-uC1.77 (PA15)
FLASH_SCK: Flash1.6 (CLK), STM32F407-uC1.89 (PB3)
FLASH_SDI: Flash1.5 (DI/IO_{0}), STM32F407-uC1.91 (PB5)
FLASH_SDO: Flash1.2 (DO/IO_{1}), STM32F407-uC1.90 (PB4)
GND: 8M-Y1.2, 8M-Y1.4, BT0.SH (B), C1.2, C2.2, C5.2, C6.2, C7.2, C8.2, C9.2, C10.2, C11.2, C12.2, C13.2, C14.2, C25.2, C26.2, C31.2, Flash1.4 (GND), LDO-1.1 (GND), R1.2, R13.2, R14.2, RST1.2, RST1.SH (B), STM32F407-uC1.10 (VSS), STM32F407-uC1.20 (VSSA), STM32F407-uC1.27 (VSS), STM32F407-uC1.74 (VSS), STM32F407-uC1.99 (VSS), TagConnect-1.5 (GND), USBC-1.A1 (GND), USBC-1.A12 (GND), USBC-1.B1 (GND), USBC-1.B12 (GND), USBC-1.S1 (SHIELD); also elsewhere on the board
HSE_OSC_IN: 8M-Y1.1, STM32F407-uC1.12 (PH0)
HSE_OSC_OUT: 8M-Y1.3, STM32F407-uC1.13 (PH1)
I2C1_SCL: STM32F407-uC1.92 (PB6); also elsewhere on the board
I2C1_SDA: STM32F407-uC1.93 (PB7); also elsewhere on the board
I2C2_SCL: STM32F407-uC1.47 (PB10); also elsewhere on the board
I2C2_SDA: STM32F407-uC1.48 (PB11); also elsewhere on the board
LED1: STM32F407-uC1.59 (PD12); also elsewhere on the board
LED2: STM32F407-uC1.60 (PD13); also elsewhere on the board
LED3: STM32F407-uC1.61 (PD14); also elsewhere on the board
LED4: STM32F407-uC1.62 (PD15); also elsewhere on the board
LED_WS2812: STM32F407-uC1.58 (PD11); also elsewhere on the board
LSE_OSC_IN: 32K-Y2.1, C5.1, STM32F407-uC1.8 (PC14)
LSE_OSC_OUT: 32K-Y2.2, C6.1, STM32F407-uC1.9 (PC15)
MOSFET_1: STM32F407-uC1.97 (PE0); also elsewhere on the board
MOSFET_2: STM32F407-uC1.98 (PE1); also elsewhere on the board
MOSFET_3: STM32F407-uC1.1 (PE2); also elsewhere on the board
MOSFET_4: STM32F407-uC1.2 (PE3); also elsewhere on the board
MOSFET_5: STM32F407-uC1.3 (PE4); also elsewhere on the board
unnamed: R11.1, USBC-1.A7 (D-), USBC-1.B7 (D-)
unnamed: R12.1, USBC-1.A6 (D+), USBC-1.B6 (D+)
unnamed: C1.1, STM32F407-uC1.49 (VCAP_1)
unnamed: C2.1, STM32F407-uC1.73 (VCAP_2)
unnamed: R14.1, USBC-1.A5 (CC1)
unnamed: R13.1, USBC-1.B5 (CC2)
PA4_BMI270_CS: STM32F407-uC1.29 (PA4); also elsewhere on the board
PA5_SPI1_SCK: STM32F407-uC1.30 (PA5); also elsewhere on the board
PA6_SPI1_MISO: STM32F407-uC1.31 (PA6); also elsewhere on the board
PA7_SPI1_MOSI: STM32F407-uC1.32 (PA7); also elsewhere on the board
PB0_BMP390_INT: STM32F407-uC1.35 (PB0); also elsewhere on the board
PB12_BMP390_CS: STM32F407-uC1.51 (PB12); also elsewhere on the board
PB13_SPI2_SCK: STM32F407-uC1.52 (PB13); also elsewhere on the board
PC2_SPI2_MISO: STM32F407-uC1.17 (PC2); also elsewhere on the board
PC3_SPI2_MOSI: STM32F407-uC1.18 (PC3); also elsewhere on the board
PD1_BMI270_INT: STM32F407-uC1.82 (PD1); also elsewhere on the board
SDIO_CLK: STM32F407-uC1.80 (PC12); also elsewhere on the board
SDIO_CMD: STM32F407-uC1.83 (PD2); also elsewhere on the board
SDIO_D0: STM32F407-uC1.65 (PC8); also elsewhere on the board
SDIO_D1: STM32F407-uC1.66 (PC9); also elsewhere on the board
SDIO_D2: STM32F407-uC1.78 (PC10); also elsewhere on the board
SDIO_D3: STM32F407-uC1.79 (PC11); also elsewhere on the board
SERVO_PWM_1: STM32F407-uC1.39 (PE8); also elsewhere on the board
SERVO_PWM_2: STM32F407-uC1.41 (PE10); also elsewhere on the board
SERVO_PWM_3: STM32F407-uC1.43 (PE12); also elsewhere on the board
SERVO_PWM_4: STM32F407-uC1.45 (PE14); also elsewhere on the board
SWCLK: STM32F407-uC1.76 (PA14), TagConnect-1.4 (SWCLK)
SWDIO: STM32F407-uC1.72 (PA13), TagConnect-1.2 (SWDIO)
UART1_RX_PWM_A10: STM32F407-uC1.69 (PA10); also elsewhere on the board
UART1_TX_PWM_A9: STM32F407-uC1.68 (PA9); also elsewhere on the board
UART2_RX: STM32F407-uC1.26 (PA3); also elsewhere on the board
UART2_TX: STM32F407-uC1.25 (PA2); also elsewhere on the board
~RESET: C7.1, R2.2, RST1.1, STM32F407-uC1.14 (NRST), TagConnect-1.3 (~RESET)

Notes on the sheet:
128 Mbit Flash
5V & 3.3V Out
STM32F407
Debug
USB C Input
Reset and Boot
Crystals
TXC 9H03200031 Load Capacitance C_L = 12.5pF
TIM1_CH4 TIM1_BKIN
C1=C2=2*(12.5pF - 10pF) = 5pF
The STEVE board should not typically pull more than 1.5A at 5V since a connected radio would use ~1A and the rest of the board would use <500mA
The W25Q128JVSIQ is a SOIC-8 5x5mm part. The W25Q128JVPIQ is a WSON-8 6x5mm part. KiCad has footprints for both
ADC
C1=C2=2*(C_L - C_stray)
NOTE: for this specific board, the following STM32 microcontrollers are drop in: (assuming a matching footprint/package is used) STM32F405 STM32F415 STM32F417
VREF+ can be directly connected to VDDA See DS8626_STM32F40xxx datasheet - Figure 51 and Figure 52 for more details
PD12, PD13, PD14, and PD15 correspond to LED4, LED3, LED5 and LED6 on the STM32F407G-DISC1. 4->1, 3->2, 5->3, 6->4
Assuming that C_stray = 10pF instead of the "rule of thumb" 5pF
TIM1_CH3N TIM1_CH3
TIM1_CH1N TIM1_CH1
Additional VSS Pins on this footprint MUST be connected to GND. See DS8626_STM32F407xx datasheet - Section 5.2 Absolute maximum ratings - Table 11 "All main power (VDD, VDDA) and ground (VSS, VSSA) pins must always be connected to the external power supply, in the permitted range"
[Generic C_stray DON'T USE] C1=C2=2*(12.5pF - 5pF) = 15pF
C1=C2=2*(10pF - 10pF) = 0pF
[Table 48] Cio=5pF
Pins 27, 74, 99 manually added to symbol
Yajingxin TAXM8M4RDBCCT2T Load Capacitance C_L = 10pF
Use USB_C_Receptacle_GCT_USB4105 -xx-A_16P_TopMnt_Horizontal Footprint and corresponding GCT connector if available. The HCTL connector is acceptable but not preferred (due to not being on Digikey).
Decoupling capacitors should be placed close to microcontroller VDD pins
[Generic C_stray DON'T USE] C1=C2=2*(10pF - 5pF) = 10pF
PE5 and PE6 on TIM9. TIM9 can allegedly do PWM output
DS8626_STM32F407xx datasheet - Page 102 - Table 32 10 pF can be used as a rough estimate of the combined pin and board capacitance
[Table 30/31] Cin(HSE)=5pF Cin(LSE)=5pF
[LINK] Calculate C values for each crystal
TIM1_CH2N TIM1_CH2

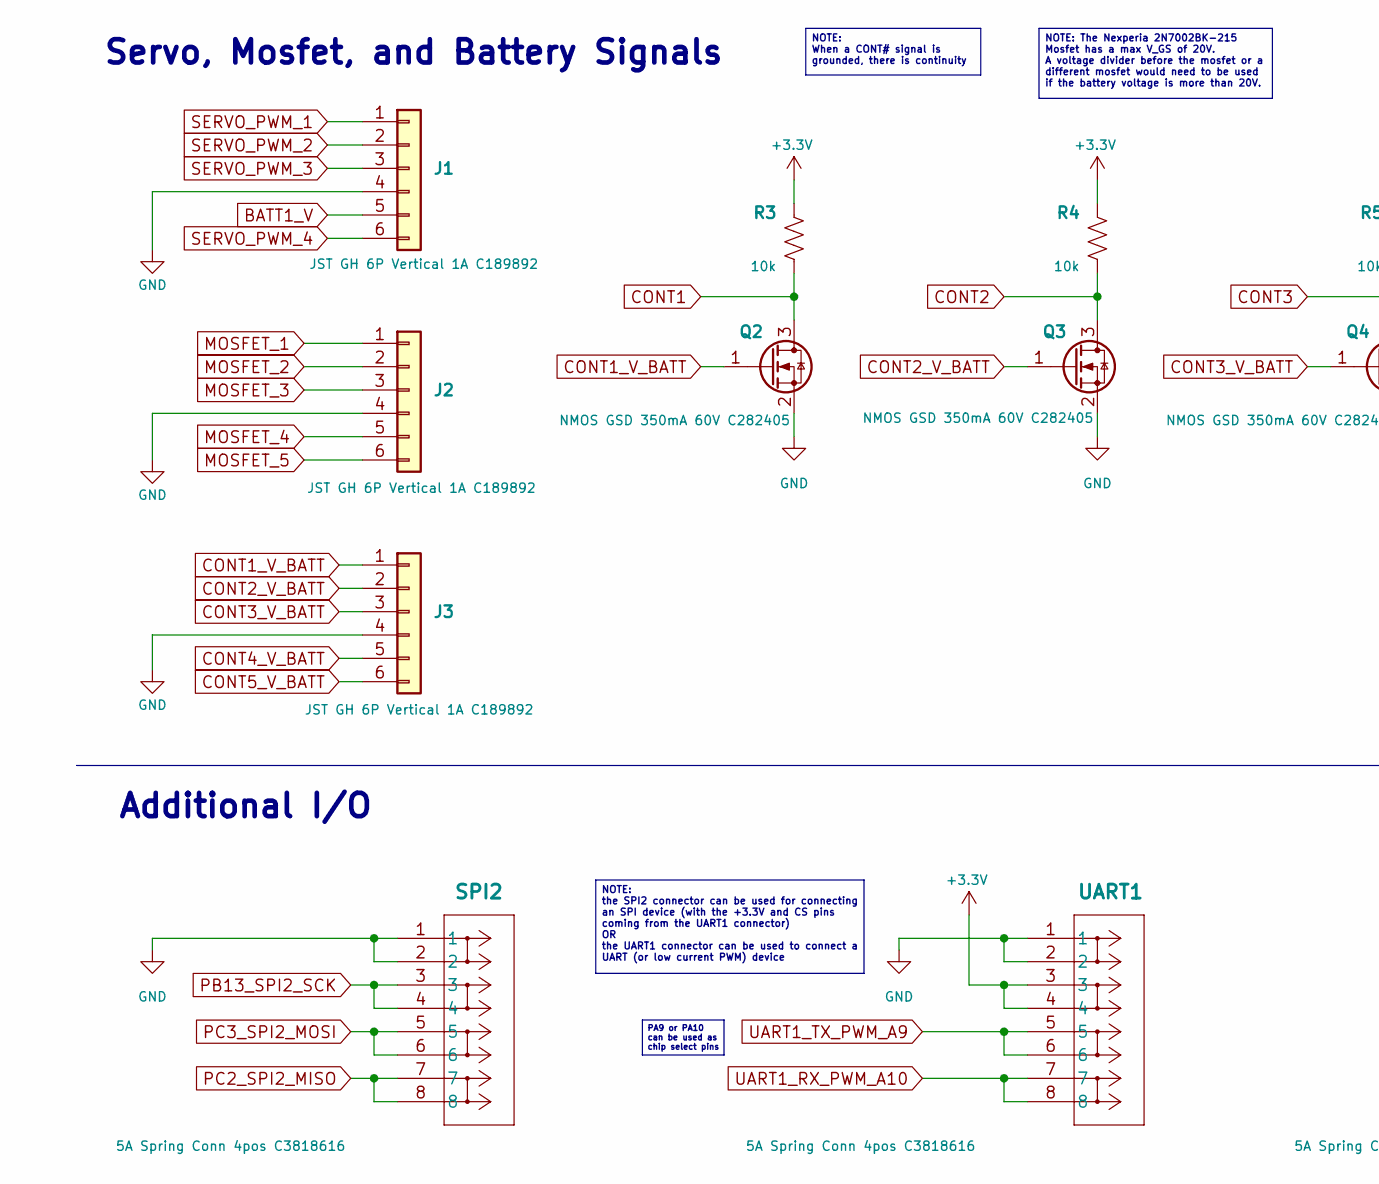
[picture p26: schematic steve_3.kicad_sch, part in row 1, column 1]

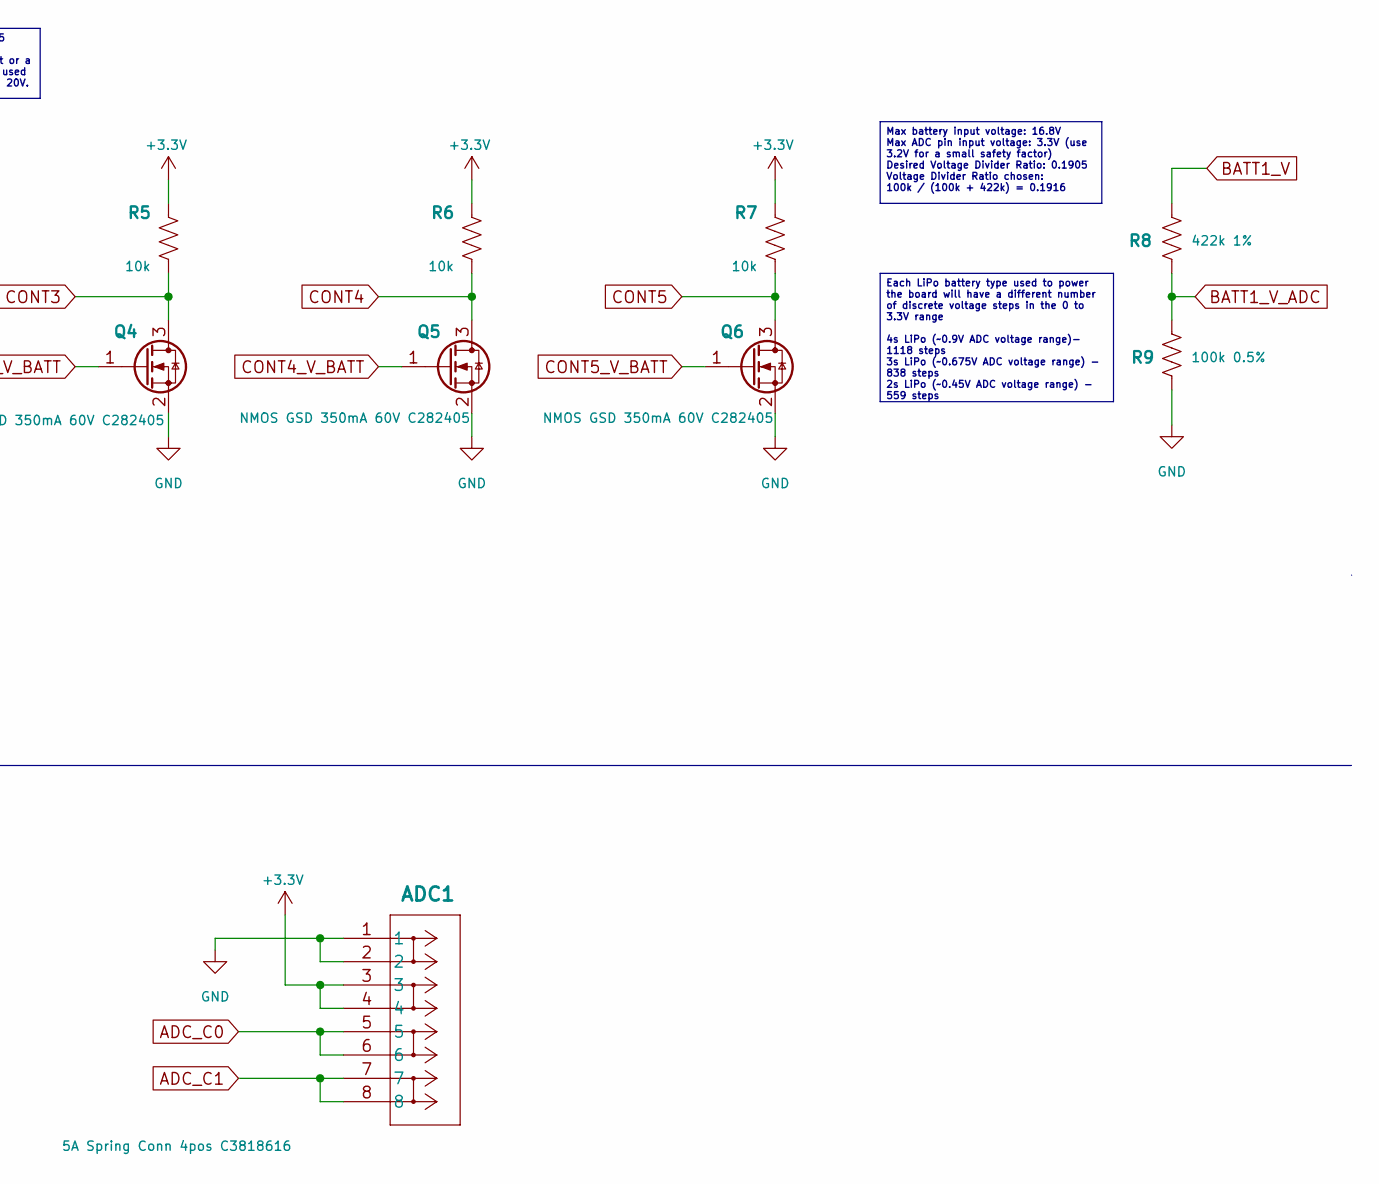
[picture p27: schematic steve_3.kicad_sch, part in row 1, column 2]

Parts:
ADC1: 5A Spring Conn 4pos C3818616; CONN_1814582_TerminalBlock_1770979_4pos_Vertical
J1, J2, J3: JST GH 6P Vertical 1A C189892; JST_GH_BM06B-GHS-TBT_1x06-1MP_P1.25mm_Vertical
Q2, Q3, Q4, Q5, Q6: NMOS GSD 350mA 60V C282405; SOT-23
R3, R4, R5, R6, R7: 10k; R_0603_1608Metric
R8: 422k 1%; R_0603_1608Metric
R9: 100k 0.5%; R_0603_1608Metric
SPI2: 5A Spring Conn 4pos C3818616; CONN_1814582_TerminalBlock_1770979_4pos_Vertical
UART1: 5A Spring Conn 4pos C3818616; CONN_1814582_TerminalBlock_1770979_4pos_Vertical

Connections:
+3.3V: ADC1.3, ADC1.4, R3.2, R4.2, R5.2, R6.2, R7.2, UART1.3, UART1.4; also elsewhere on the board
ADC_C0: ADC1.5, ADC1.6; also elsewhere on the board
ADC_C1: ADC1.7, ADC1.8; also elsewhere on the board
BATT1_V: J1.5, R8.2
BATT1_V_ADC: R8.1, R9.2; also elsewhere on the board
CONT1: Q2.3 (D), R3.1; also elsewhere on the board
CONT1_V_BATT: J3.1, Q2.1 (G)
CONT2: Q3.3 (D), R4.1; also elsewhere on the board
CONT2_V_BATT: J3.2, Q3.1 (G)
CONT3: Q4.3 (D), R5.1; also elsewhere on the board
CONT3_V_BATT: J3.3, Q4.1 (G)
CONT4: Q5.3 (D), R6.1; also elsewhere on the board
CONT4_V_BATT: J3.5, Q5.1 (G)
CONT5: Q6.3 (D), R7.1; also elsewhere on the board
CONT5_V_BATT: J3.6, Q6.1 (G)
GND: ADC1.1, ADC1.2, J1.4, J2.4, J3.4, Q2.2 (S), Q3.2 (S), Q4.2 (S), Q5.2 (S), Q6.2 (S), R9.1, SPI2.1, SPI2.2, UART1.1, UART1.2; also elsewhere on the board
MOSFET_1: J2.1; also elsewhere on the board
MOSFET_2: J2.2; also elsewhere on the board
MOSFET_3: J2.3; also elsewhere on the board
MOSFET_4: J2.5; also elsewhere on the board
MOSFET_5: J2.6; also elsewhere on the board
PB13_SPI2_SCK: SPI2.3, SPI2.4; also elsewhere on the board
PC2_SPI2_MISO: SPI2.7, SPI2.8; also elsewhere on the board
PC3_SPI2_MOSI: SPI2.5, SPI2.6; also elsewhere on the board
SERVO_PWM_1: J1.1; also elsewhere on the board
SERVO_PWM_2: J1.2; also elsewhere on the board
SERVO_PWM_3: J1.3; also elsewhere on the board
SERVO_PWM_4: J1.6; also elsewhere on the board
UART1_RX_PWM_A10: UART1.7, UART1.8; also elsewhere on the board
UART1_TX_PWM_A9: UART1.5, UART1.6; also elsewhere on the board

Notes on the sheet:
Servo, Mosfet, and Battery Signals
Additional I/O
NOTE: the SPI2 connector can be used for connecting an SPI device (with the +3.3V and CS pins coming from the UART1 connector) OR the UART1 connector can be used to connect a UART (or low current PWM) device
NOTE: When a CONT# signal is grounded, there is continuity
PA9 or PA10 can be used as chip select pins
Max battery input voltage: 16.8V Max ADC pin input voltage: 3.3V (use 3.2V for a small safety factor) Desired Voltage Divider Ratio: 0.1905 Voltage Divider Ratio chosen: 100k / (100k + 422k) = 0.1916
NOTE: The Nexperia 2N7002BK-215 Mosfet has a max V_GS of 20V. A voltage divider before the mosfet or a different mosfet would need to be used if the battery voltage is more than 20V.
Each LiPo battery type used to power the board will have a different number of discrete voltage steps in the 0 to 3.3V range 4s LiPo (~0.9V ADC voltage range)- 1118 steps 3s LiPo (~0.675V ADC voltage range) - 838 steps 2s LiPo (~0.45V ADC voltage range) - 559 steps

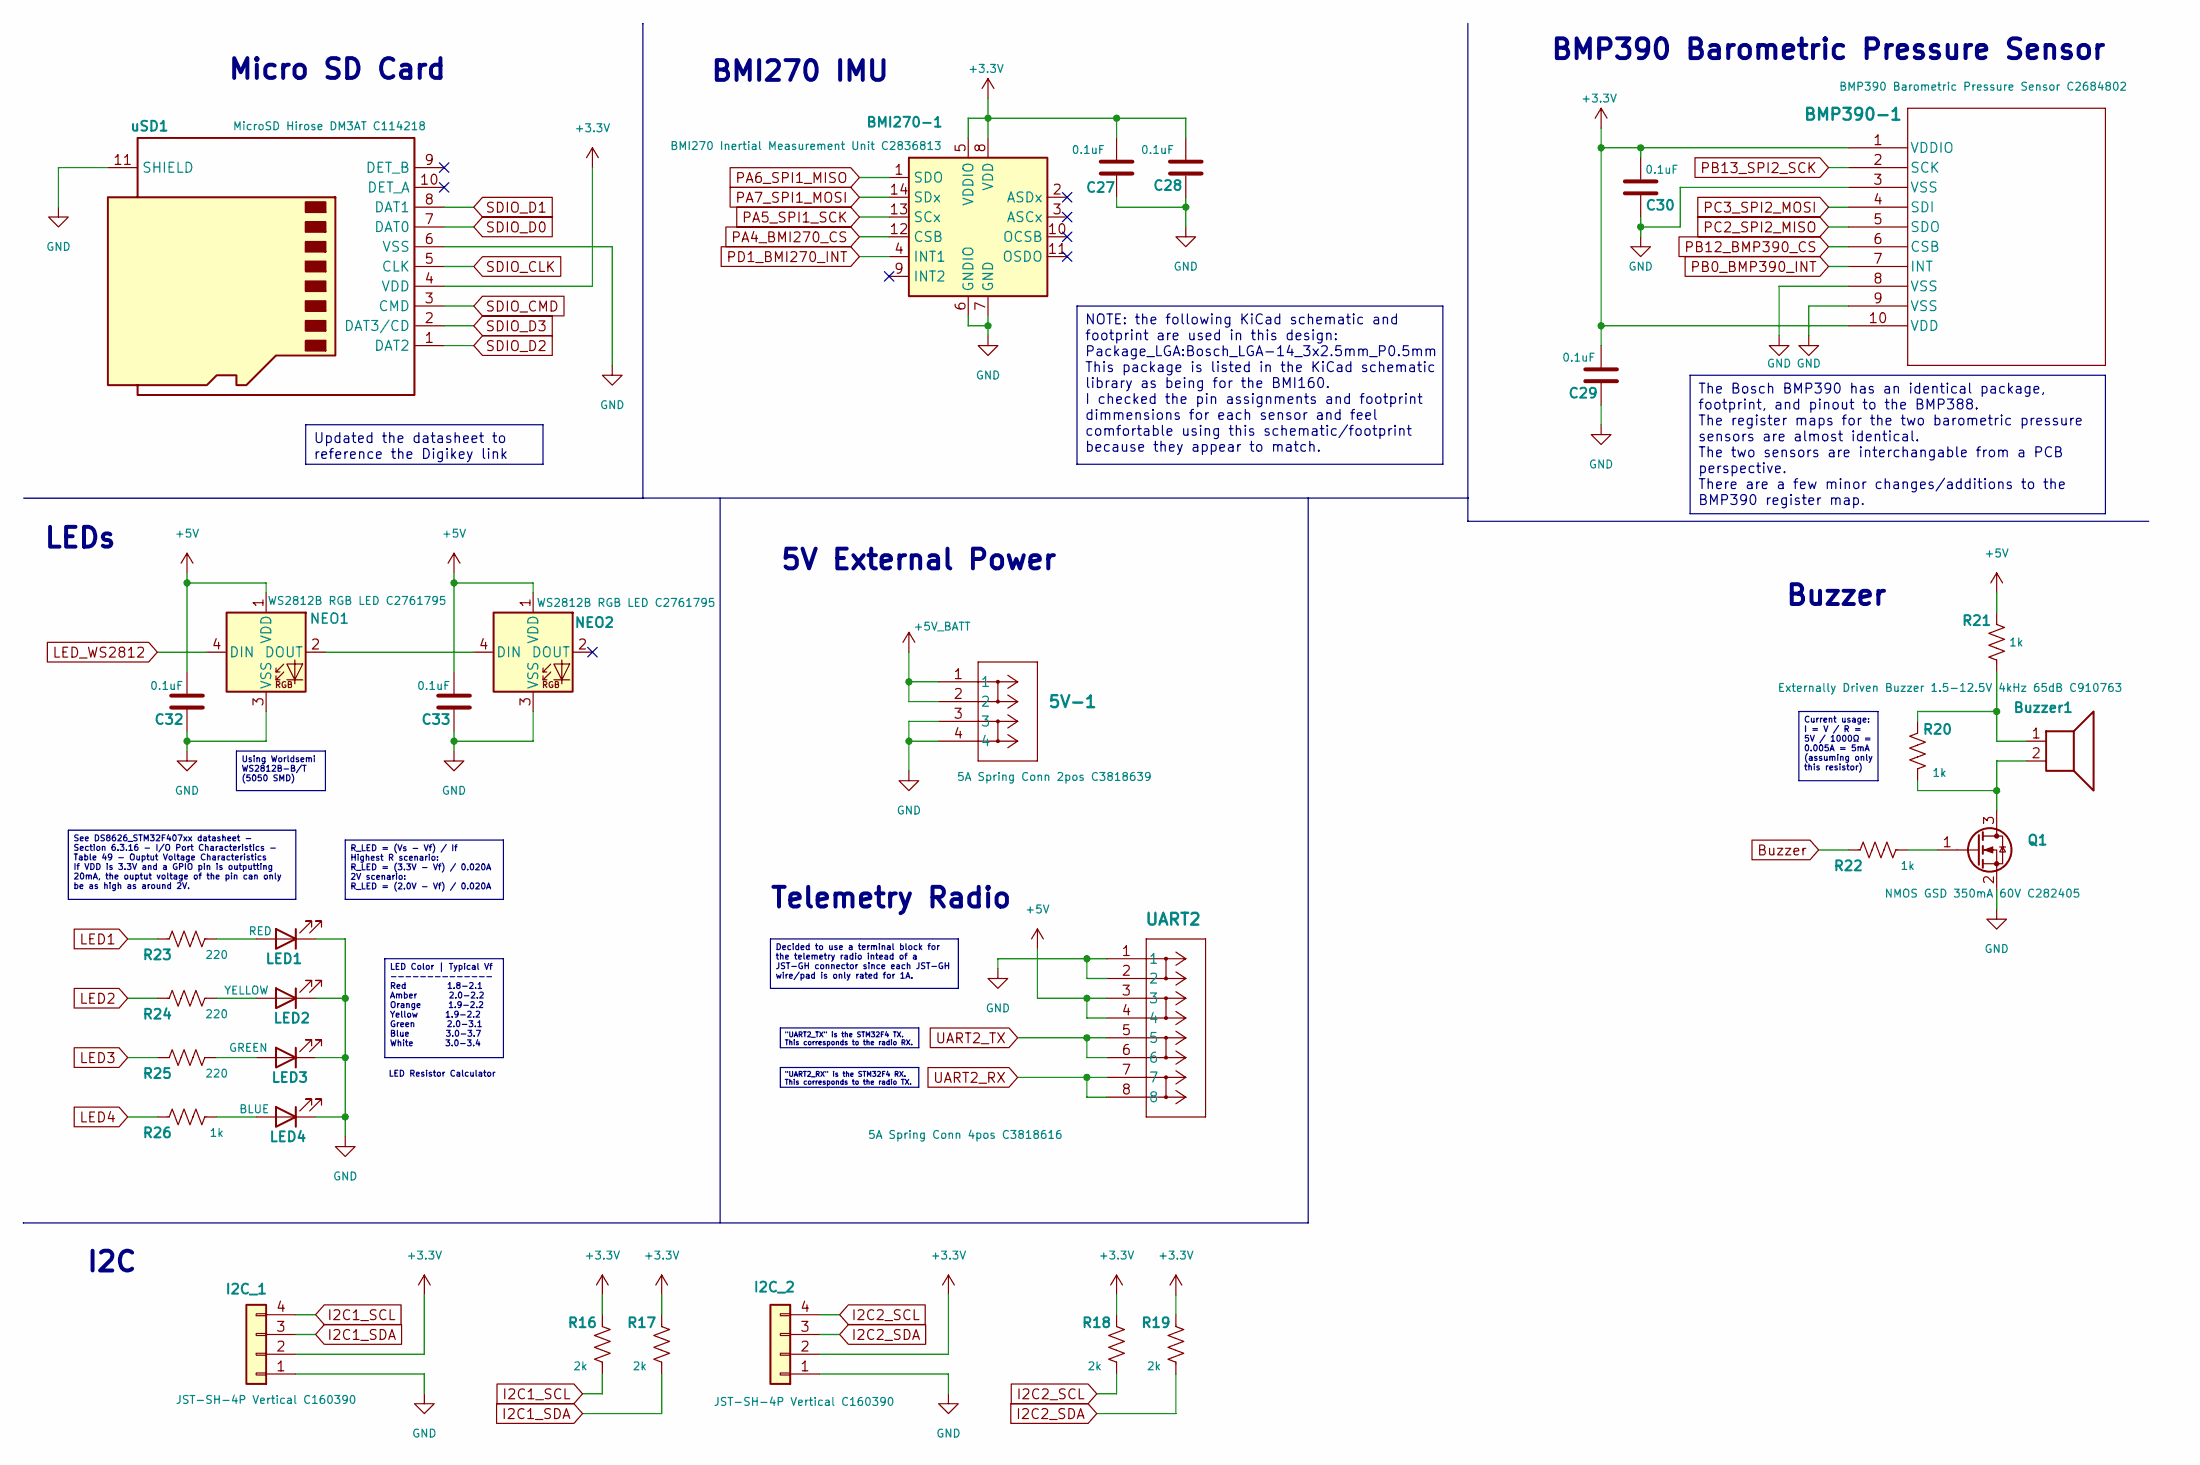
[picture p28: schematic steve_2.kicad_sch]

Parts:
5V-1: 5A Spring Conn 2pos C3818639; CONN_1814498_TerminalBlock-1770885-2pos
BMI270-1: BMI270 Inertial Measurement Unit C2836813; Bosch_LGA-14_3x2.5mm_P0.5mm
BMP390-1: BMP390 Barometric Pressure Sensor C2684802; QFN_BMP388_BOS
Buzzer1: Externally Driven Buzzer 1.5-12.5V 4kHz 65dB C910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; Buzzer_Murata_PKMCS0909E
C27, C28, C29, C30, C32, C33: 0.1uF; C_0603_1608Metric
I2C_1, I2C_2: JST-SH-4P Vertical C160390; JST-SH_BM04B-SRSS-TB_1x04_Vertical_P1.00mm
LED1: RED; LED_0603_1608Metric
LED2: YELLOW; LED_0603_1608Metric
LED3: GREEN; LED_0603_1608Metric
LED4: BLUE; LED_0603_1608Metric
NEO1, NEO2: WS2812B RGB LED C2761795; LED_WS2812B_PLCC4_5.0x5.0mm_P3.2mm
Q1: NMOS GSD 350mA 60V C282405; SOT-23
R16, R17, R18, R19: 2k; R_0603_1608Metric
R20, R21, R22, R26: 1k; R_0603_1608Metric
R23, R24, R25: 220; R_0603_1608Metric
UART2: 5A Spring Conn 4pos C3818616; CONN_1814582_TerminalBlock_1770979_4pos_Vertical
uSD1: MicroSD Hirose DM3AT C114218; microSD_3D_HC_Hirose_DM3AT-SF-PEJM5

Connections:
+3.3V: BMI270-1.5 (VDDIO), BMI270-1.8 (VDD), BMP390-1.1 (VDDIO), BMP390-1.10 (VDD), C27.1, C28.1, C29.1, C30.1, I2C_1.2, I2C_2.2, R16.2, R17.2, R18.2, R19.2, uSD1.4 (VDD); also elsewhere on the board
+5V: C32.1, C33.1, NEO1.1 (VDD), NEO2.1 (VDD), R21.2, UART2.3, UART2.4; also elsewhere on the board
+5V_BATT: 5V-1.1, 5V-1.2; also elsewhere on the board
Buzzer: R22.1; also elsewhere on the board
GND: 5V-1.3, 5V-1.4, BMI270-1.6 (GNDIO), BMI270-1.7 (GND), BMP390-1.3 (VSS), BMP390-1.8 (VSS), BMP390-1.9 (VSS), C27.2, C28.2, C29.2, C30.2, C32.2, C33.2, I2C_1.1, I2C_2.1, LED1.1 (K), LED2.1 (K), LED3.1 (K), LED4.1 (K), NEO1.3 (VSS), NEO2.3 (VSS), Q1.2 (S), UART2.1, UART2.2, uSD1.6 (VSS), uSD1.11 (SHIELD); also elsewhere on the board
I2C1_SCL: I2C_1.4, R16.1; also elsewhere on the board
I2C1_SDA: I2C_1.3, R17.1; also elsewhere on the board
I2C2_SCL: I2C_2.4, R18.1; also elsewhere on the board
I2C2_SDA: I2C_2.3, R19.1; also elsewhere on the board
LED1: R23.1; also elsewhere on the board
LED2: R24.1; also elsewhere on the board
LED3: R25.1; also elsewhere on the board
LED4: R26.1; also elsewhere on the board
LED_WS2812: NEO1.4 (DIN); also elsewhere on the board
unnamed: Buzzer1.1, R20.2, R21.1
unnamed: LED1.2 (A), R23.2
unnamed: LED2.2 (A), R24.2
unnamed: LED3.2 (A), R25.2
unnamed: LED4.2 (A), R26.2
unnamed: NEO1.2 (DOUT), NEO2.4 (DIN)
unnamed: Buzzer1.2, Q1.3 (D), R20.1
unnamed: Q1.1 (G), R22.2
PA4_BMI270_CS: BMI270-1.12 (CSB); also elsewhere on the board
PA5_SPI1_SCK: BMI270-1.13 (SCx); also elsewhere on the board
PA6_SPI1_MISO: BMI270-1.1 (SDO); also elsewhere on the board
PA7_SPI1_MOSI: BMI270-1.14 (SDx); also elsewhere on the board
PB0_BMP390_INT: BMP390-1.7 (INT); also elsewhere on the board
PB12_BMP390_CS: BMP390-1.6 (CSB); also elsewhere on the board
PB13_SPI2_SCK: BMP390-1.2 (SCK); also elsewhere on the board
PC2_SPI2_MISO: BMP390-1.5 (SDO); also elsewhere on the board
PC3_SPI2_MOSI: BMP390-1.4 (SDI); also elsewhere on the board
PD1_BMI270_INT: BMI270-1.4 (INT1); also elsewhere on the board
SDIO_CLK: uSD1.5 (CLK); also elsewhere on the board
SDIO_CMD: uSD1.3 (CMD); also elsewhere on the board
SDIO_D0: uSD1.7 (DAT0); also elsewhere on the board
SDIO_D1: uSD1.8 (DAT1); also elsewhere on the board
SDIO_D2: uSD1.1 (DAT2); also elsewhere on the board
SDIO_D3: uSD1.2 (DAT3/CD); also elsewhere on the board
UART2_RX: UART2.7, UART2.8; also elsewhere on the board
UART2_TX: UART2.5, UART2.6; also elsewhere on the board

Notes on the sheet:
BMP390 Barometric Pressure Sensor
Micro SD Card
LEDs
BMI270 IMU
5V External Power
LED Resistor Calculator
Buzzer
Telemetry Radio
I2C
LED Color | Typical Vf -------------- Red 1.8-2.1 Amber 2.0-2.2 Orange 1.9-2.2 Yellow 1.9-2.2 Green 2.0-3.1 Blue 3.0-3.7 White 3.0-3.4
See DS8626_STM32F407xx datasheet - Section 6.3.16 - I/O Port Characteristics - Table 49 - Ouptut Voltage Characteristics If VDD is 3.3V and a GPIO pin is outputting 20mA, the ouptut voltage of the pin can only be as high as around 2V.
Using Worldsemi WS2812B-B/T (5050 SMD)
Decided to use a terminal block for the telemetry radio intead of a JST-GH connector since each JST-GH wire/pad is only rated for 1A.
"UART2_TX" is the STM32F4 TX. This corresponds to the radio RX.
Current usage: I = V / R = 5V / 1000Ω = 0.005A = 5mA (assuming only this resistor)
NOTE: the following KiCad schematic and footprint are used in this design: Package_LGA:Bosch_LGA-14_3x2.5mm_P0.5mm This package is listed in the KiCad schematic library as being for the BMI160. I checked the pin assignments and footprint dimmensions for each sensor and feel comfortable using this s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
Updated the datasheet to reference the Digikey link
"UART2_RX" is the STM32F4 RX. This corresponds to the radio TX.
The Bosch BMP390 has an identical package, footprint, and pinout to the BMP388. The register maps for the two barometric pressure sensors are almost identical. The two sensors are interchangable from a PCB perspective. There are a few minor changes/additions to the BMP390 register map.
R_LED = (Vs - Vf) / If Highest R scenario: R_LED = (3.3V - Vf) / 0.020A 2V scenario: R_LED = (2.0V - Vf) / 0.020A

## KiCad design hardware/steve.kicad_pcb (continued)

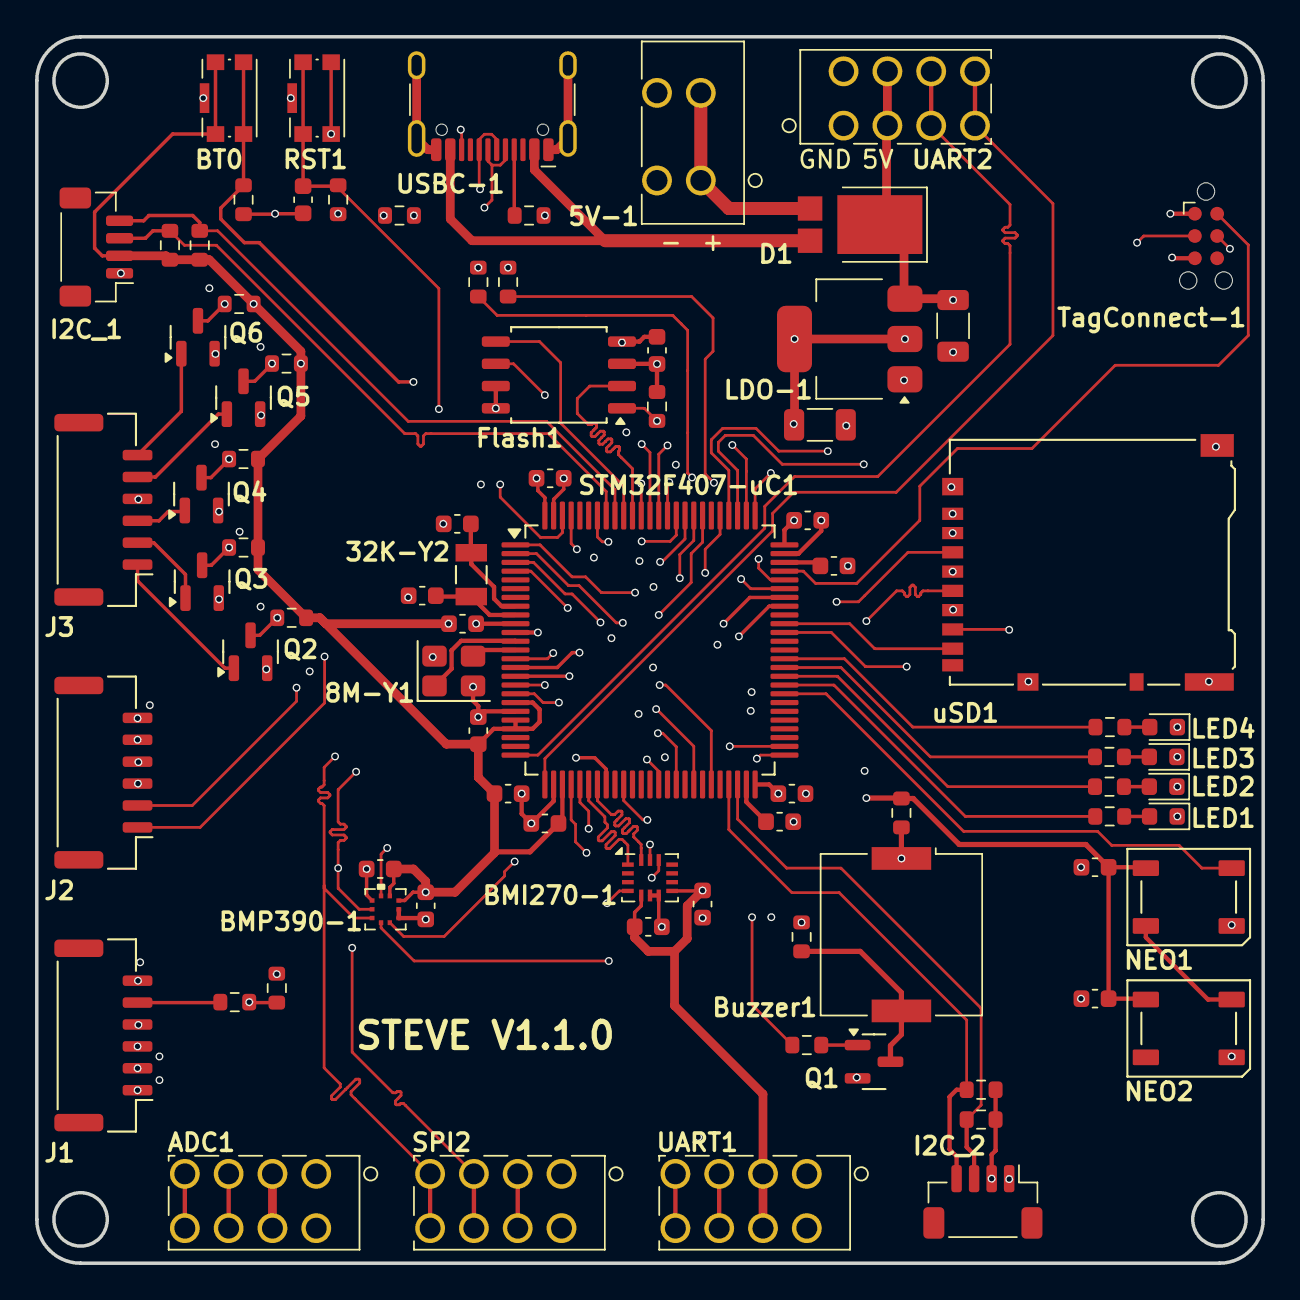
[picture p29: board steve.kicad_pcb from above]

Board: 6 copper layers, 70.0 x 70.0 mm, 82 parts (0 on the bottom side), 86 nets.

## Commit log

2024-09-30 Added STEVE summary, started schematic
    Added STEVE info section to README. Added STEVE V1 Planned Hardware list to README. Started board schematic using KiCad STM32F407VG 100 pin footprint
    [steve.kicad_pcb, steve.kicad_sch]
2024-10-06 Added 5V reg and other components
    Added 5V regulator circuit to schematic. Added project libraries for imported symbols and footprints. Added additional components to schematic.
    [1-2834015-4.step, RJN0012A.stp, steve.kicad_pcb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]
2025-04-06 import BMP388, add BMP388 to pcb and sch
    Import BMP388 symbol and footprint to project imports dir. Add BMP388 symbol to schematic and footprint to pcb.
    [QFN_BMP388_BOS.step, steve.kicad_pcb, steve.kicad_sch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]
2025-04-13 Finished sensor, flash, and SD card in schematic; Updated README for remaining items
    Finished BMI270 and BMP390, Flash storage, and microSD card in schematic; Updated README for remaining items
    [steve.kicad_pcb, steve.kicad_sch, steve_2.kicad_sch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]
2025-04-14 Add components to schematic; fix existing ones
    Added additional components to schematic such as IO connectors. Replaced the 10A TO-263-2 diode rectifiers with much smaller 5A ones.
    Other various fixes.
    [BM04B-SRSS-TB.STEP, JST-GH-6P-Side_SM06B-GHS-TB.STEP, JST-GH-6P-Vertical_BM06B-GHS-TBT.STEP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]
2025-04-19 Added buzzer and LEDs to schematic
    Added buzzer and LEDs (4 regular and 2 WS2812B) to schematic. Minor schematic fixes such as PMIC enable pin voltage divider.
    [steve.kicad_pcb, steve.kicad_sch, steve_2.kicad_sch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]
2025-04-20 Removed PSM board components; added power conn; fixed telem conn
    Moved PSM board components to the PSM board schematic.
    Added a connector for the regulated 5V input to STEVE that comes from the PSM board.
    Changed the radio telemetry connector to a 4 pin screwless terminal block to mitigate current limit concerns with the previous connector.
    [1770885.stp, 1770979.STEP, steve.kicad_pcb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]
2025-04-27 Finished schematic
    Finished schematic - 3D model fixes using custom imports, all important parts sourced, additional GPIO/bus pins broken out, PSM board signals broken out, battery voltage sense line added.
    [DM3AT-SF-PEJM5.STEP, KMR221G LFS.STEP, steve.kicad_pcb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]
2025-05-04 started component layout
    started component layout - attempting to use a 60x60mm board size
    [steve.kicad_pcb, steve.kicad_sch, steve_2.kicad_sch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]
2025-05-08 finished initial component layout
    [steve.kicad_pcb]
2025-05-08 update flash chip 3D model; update to KiCad 9.0.2
    update flash chip 3D model with the new name used in KiCad 9.0.2
    Updated project to KiCad 9.0.2 (latest version)
    [steve.kicad_pcb, steve.kicad_sch, steve_2.kicad_sch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]
2025-05-12 use 50x50mm board
    [steve.kicad_pcb]
2025-05-12 Add schematic PDF
    Add schematic PDF to newly created share folder in
    CURRENT_PROJECT_DIR/hardware
2025-05-13 started routing the PCB
    started routing the PCB - some components moved a bit. Added GND fill/pour on top and bottom planes, adding extra GND trace width where needed. Also routed short power traces on the top layer. The USB-C 5V trace is a bit long and might need to be moved to layer 2 at some point, but that would require a 70mil trace instead of a 14mil trace for handling 1.5A on an inner layer that is thinner.
    [steve.kicad_pcb]
2025-05-14 added first length matched SPI sets
    added first length matched SPI sets for the Flash chip and the BMI270. Still need to finish routing the BMI270 and other footprints that use SPI
    [steve.kicad_pcb]
2025-05-18 Finished routing traces
    Finished routing traces. Also added extra ground vias to stitch the ground planes together. Lessons for next time: power pads (on a microcontroller or other) should immediately get a via; passives ca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
    [steve.kicad_pcb, steve.kicad_sch, steve_2.kicad_sch]
2025-05-18 Increase text to 1mm
    Increase text length/width to 1mm and line thickness to 0.153mm to match fab capabilities and rules. All capacitor and resistor designators have been hidden to reduce silkscreen clutter.
    [steve.kicad_pcb]
2025-05-24 Added Custom Design Rules for JLC; fixed DRC errors
    Added Custom Design Rules for JLC based on a community created custom ruleset.
    Fixed DRC errors that the custom JLC rules pointed out. Updated project constraints to not throw extra errors.
    [steve.kicad_pcb]
2025-05-24 Add text to board
    Add text to board silkscreen
    [steve.kicad_pcb]
2025-05-24 Generated JLC production files
    Generated JLC production files using the "Fabrication Toolkit" (JLC) plugin
    STEVE_1.0.0.zip created
    BOM and Placement CSVs also created, but not included due to the gitignore
2025-05-24 Schematic and Board fixes for Mfg
    Schematic and Board fixes for Manufacturing. Added LCSC/JLC part numbers to values in schematic for BOM processing. Updated schematic fields. Added GND to each PSM connector. Brought PSM connector fix to PCB. Updated PCB designator locations from schematic changes.
    [steve.kicad_pcb, steve.kicad_sch, steve_2.kicad_sch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]
2025-05-25 Updated production files
    Generated new production files now that all major components have a JLC part number added to their value and the J1-J3 connectors have been changed.
2025-05-25 Add JLC Quote data for STEVE V1.0.0
    Save screenshots of all JLC quote line items for ordering STEVE V1.0.0
    Does not include the true cost of all major components since many were purchased separately before this point.
    Also does not include the possible price of "baking" AKA drying the WS2812 LEDs (~$7.50).
    Readme updated.
2025-05-25 Add STEVE V1.0.0 board pictures to share folder
    Add STEVE V1.0.0 board pictures to share/STEVE_V1.0.0 folder
2025-05-25 Regenerated STEVE V1.0.0 Schematic
    Regenerated STEVE V1.0.0 Schematic (since it was updated a bit). Moved the schematic to the STEVE_V1.0.0 folder
2025-05-25 Fixed all ERC issues; fixed important DRC issues
    Fixed all ERC Errors and Warnings in the schematic. Fixed all Errors and Warnings in the DRC for the board (Not counting JLC 4-Wire Kelvin test and plane thermal relief spoke errors that were manually reviewed and excluded).
    [steve.kicad_pcb, steve.kicad_sch, steve_2.kicad_sch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]
2025-05-30 Update board to 6 layers and single sided assembly
    Update board to 6 layers and single sided assembly (all components placed on the same side); all footprints given an initial placement
    [steve.kicad_pcb]
2025-06-01 Routed 6 layer board; DRC passes
    Finished routing the 6 layer board; All DRC issues resolved
    [steve.kicad_pcb]
2025-06-01 Created STEVE footprint; added image to PCB
    Created STEVE image footprint with KiCad bitmap image tool; added footprint to imported footprints library; manually added new footprint to PCB.
    [steve.kicad_pcb]
2025-06-01 Generated STEVE 1.1.0 production files
    Generated STEVE 1.1.0 production files; files in hardware/production/STEVE-1.1.0
    [steve.kicad_pcb]
2025-06-01 Update gitignore to allow csv files to be saved
    Update gitignore to allow csv files to be saved.
    STEVE 1.0.0 and 1.1.0 csv files are now tracked.
    [bom.csv, designators.csv, positions.csv]
2025-06-01 Add STEVE 1.1.0 Schematic PDF and board pictures
    Add STEVE 1.1.0 Schematic PDF and board pictures (renders from 3D viewer)
2025-06-01 Added costed down bom and positions files
    Added costed down bom and positions files. The costed_down_1 csv files have the easy through-hole components removed, specifically the screwless terminal blocks
    [bom_costed_down_1.csv, positions_costed_down_1.csv]
